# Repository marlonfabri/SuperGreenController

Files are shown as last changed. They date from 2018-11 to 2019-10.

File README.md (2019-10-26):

SuperGreenLab

SuperGreenLab (https://www.reddit.com/r/SuperGreenLab)

# Table of Contents

   * [SuperGreenController](#supergreencontroller)
   * [Board Overview](#board-overview)
   * [Outputs](#outputs)
      * [Light and AC](#light-and-ac)
      * [Motors](#motors)
      * [Sensors](#sensors)
      * [Power considerations](#power-considerations)
   * [License](#license)
   * [Creative Commons Warranties Disclaimer](#creative-commons-warranties-disclaimer)

# SuperGreenController

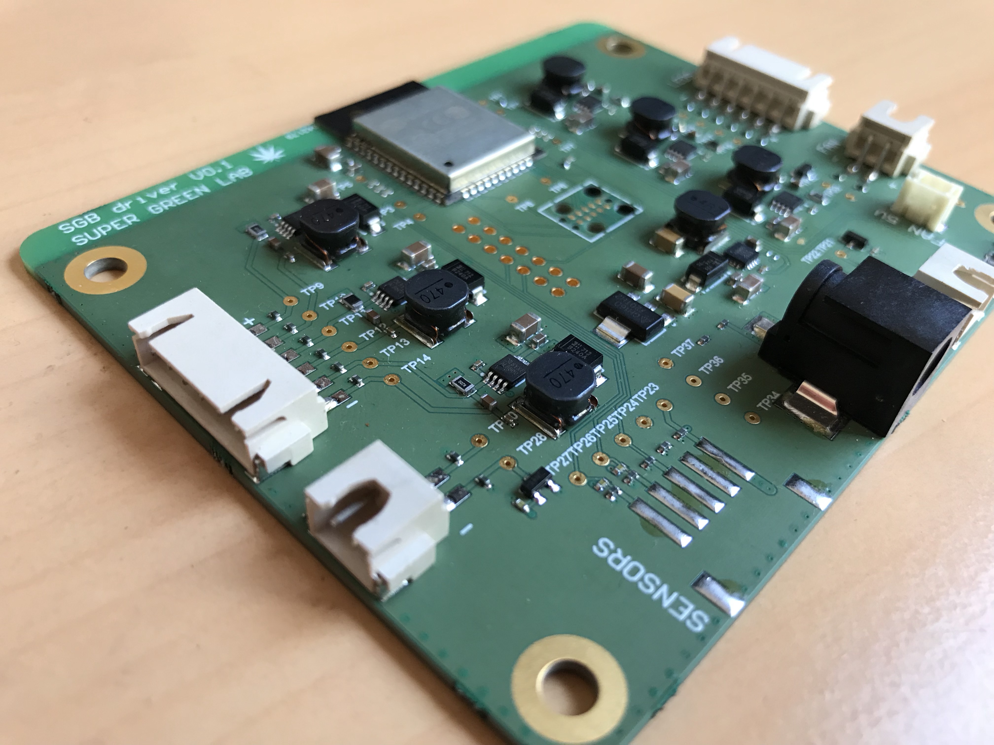
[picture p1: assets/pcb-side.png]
SuperGreenLed

V1.0 Prototype

Connected grow box controller with 6 light/AC control output (10V analog), 3 Motors output (24V/1A) and 3 sensors ports (I2C) from supergreenlab (https://supergreenlab.com/). This open hardware design is licensed under the Creative Commons Attribution-ShareAlike 3.0 Unported License.

Pull requests of relevant issues are warmly welcomed.

# Board Overview

* **MCU** : [ESP32-WROOM-32](https://www.espressif.com/en/products/hardware/esp-wroom-32/overview), wifi , bluetooth and BLE microcontroller. Fimrware : [SuperGreenOS](https://github.com/supergreenlab/SuperGreenOS) app : [SuperGreenApp](https://github.com/supergreenlab/SuperGreenApp)
* **Light/AC OUTPUTS** : 6x 0-10V Analog output (3.3V->10V done using [LM358](https://www.diodes.com/assets/Datasheets/LM358.pdf) op amp). Connector : [S3B-XH-SM4-TB](http://www.jst-mfg.com/product/detail_e.php?series=277)
* **MOTOR OUTPUTS** : 3x 24V output controlled by mosfet. Connector : [S2B-XH-SM4-TB](http://www.jst-mfg.com/product/detail_e.php?series=277)
* **SENSORS** : 1x I2C shared with embedded temperature sensor, 1x I2C shared on 2 connectors. Connector : [S4B-XH-SM4-TB](http://www.jst-mfg.com/product/detail_e.php?series=277)
* **POWER IN** : 24VDC/5A standard 5x2.5mm barrel/Jack input (Power supply : https://amzn.to/2DNSty4)
* **DCDC** : [TS30041](https://www.semtech.com/uploads/documents/ts3004x.pdf) 3.3V buck stepdown, up to 1A
* **ADDITIONAL** : 2.54 mm solderable header (additional pins and flash) JTAG and flash TAG connect interface
* **STACKUP** : standard 4 layers 1.6mm FR4 (Signal-GND-POWER-Signal)
* **SIZE** : 100mmx80mm

# OUTPUTS

## Light and AC

* **L1->L4** : Provide both power (24V) and control (0-10V). These outputs can be used to power SuperGreenBoards 36.301B (20W) and 72.301B (40W) for a max power consumption of 80W.
* **L5 & L6** : Power pin is not connected, only provide control (0-10V).

The 0-10V Analog output the Light/AC output can :
* Control any of the SGB 36.301B, 72.301B, 144.301B 
* Control a MeanWell type B or AB power supply (eg for the SGB 288.301B)
* Control any AC equipement through a [SSR relay](https://amzn.to/2DSlBoa)
* Control any device that can be driven by a 0-10V voltage

## Motors

**M1->M3** connectors are standard 2 pins JST connectors. It can be used to power 24V fans, blowers, pumps ect...

Example of compatible devices : [120mm blower](https://amzn.to/2GQcyqW) [97mm blower](https://amzn.to/2XcGl2I) [120mm fan](https://amzn.to/2GyCE26) [80mm fan](https://amzn.to/2IyqqZ4) 

## Sensors

* **S1** : 3V3 I2C port shared with embedded temperature/humidity sensor
* **S2 & S2bis** : shared 3V3 I2C bus

# POWER CONSIDERATIONS

The SuperGreenController is meant to be powered by a 24VDC/5A power supply for a total of 120W maximum.

A **10W** margin should be kept to ensure proper functionnement of the controller (this includes wifi, onboard sensors, onboard energy conversions ect.. and a large safety margin).
No more than **80W** of leds should be powered by the controller itself (2x 72.301B, 4x 36.301B or 1x 72.301B and 2x36.301B)
The rest of the energy can be used to power fans blowers and pumps.

An onboard current sensor will be used to monitor the power consumption of each device attached to the controller and determine is the power demand of the system is too high.

# License

This work is licensed under the Creative Commons Attribution-ShareAlike 3.0 Unported License. To view a copy of this license, visit http://creativecommons.org/licenses/by-sa/3.0/ or send a letter to Creative Commons, PO Box 1866, Mountain View, CA 94042, USA.

# Creative Commons Warranties Disclaimer

UNLESS OTHERWISE MUTUALLY AGREED TO BY THE PARTIES IN WRITING, LICENSOR OFFERS THE WORK AS-IS AND MAKES NO REPRESENTATIONS OR WARRANTIES OF ANY KIND CONCERNING THE WORK, EXPRESS, IMPLIED, STATUTORY OR OTHERWISE, INCLUDING, WITHOUT LIMITATION, WARRANTIES OF TITLE, MERCHANTIBILITY, FITNESS FOR A PARTICULAR PURPOSE, NONINFRINGEMENT, OR THE ABSENCE OF LATENT OR OTHER DEFECTS, ACCURACY, OR THE PRESENCE OF ABSENCE OF ERRORS, WHETHER OR NOT DISCOVERABLE. SOME JURISDICTIONS DO NOT ALLOW THE EXCLUSION OF IMPLIED WARRANTIES, SO SUCH EXCLUSION MAY NOT APPLY TO YOU.

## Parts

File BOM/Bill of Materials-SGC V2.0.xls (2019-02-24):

Comment | Description | Designator | Footprint | LibRef | Manufacturer | Manufacturer Part Number | Quantity
10uF | Multilayer Ceramic Capacitors MLCC - SMD/SMT 10uF 50V X5R +/-20% 1206 Gen Purp | C1, C4_L1, C4_L2, C4_L3, C5_L1, C5_L2, C5_L3, C6 | 1206 | C 10uF 50V X5R +/-20% 1206 Gen Purp | Taiyo Yuden | UMK316BBJ106ML-T | 8.0
0.1uF | Multilayer Ceramic Capacitors MLCC - SMD/SMT 100nF 50V X7R 10% | C2, C3, C7, C11 | 0603 | C 0.1uF 50V X7R 10% | Yageo | CC0603KRX7R9BB104 | 4.0
22uF | Multilayer Ceramic Capacitors MLCC - SMD/SMT 0805 25Vdc 22uF X5R 20% | C8, C9 | 0805 | C 22uF 25V X5R 20% | Murata Electronics | GRT21BR61E226ME13L | 2.0
22nF | MLCC - SMD/SMT 0.022uF 50V X7R 10% 0402 | C10 | 0402 | C 22nF 50V X7R 10% 0402 | Taiyo Yuden | UMK105B7223KV-FR | 1.0
MBR230LSFT1G | Schottky Diodes & Rectifiers 2A 30V SCHOTTKY | D1 | SOD-123LF | MBR230LSFT1G | ON Semiconductor | MBR230LSFT1G | 1.0
TAG connect |  | J1 | TC2050-IDC | TC2050 |  |  | 1.0
Header 2.54 |  | J2 | Pin header 2.54 14 contacts 2 rows | Header 2.54 |  |  | 1.0
JST XH3 |  | J3_L1, J3_L2, J3_L3, J4_L1, J4_L2, J4_L3 | JST XH-3 Right angle -SMD | S3B-XH-SM4-TB |  |  | 6.0
JST XH 2 |  | J5_M1, J5_M2, J5_M3 | JST XH-2 Right angle -SMD | S2B-XH-SM4-TB |  |  | 3.0
BARREL | CONN PWR JACK 2.5X5.5MM SOLDER | J6 | PJ-036BH-SMT-TR | PJ-036BH-SMT-TR | CUI Inc. | PJ-036BH-SMT-TR | 1.0
JST XH4 |  | J7_S1, J7_S2, J7_S3 | JST XH-4 Right angle -SMD | S4B-XH-SM4-TB |  |  | 3.0
APFA3010SEEZGKQBKC | Standard LEDs - SMD 3.0x1.0MM RA RGB SMD | L1 | APFA3010SEEZGKQBKC | APFA3010SEEZGKQBKC | Kingbright | APFA3010SEEZGKQBKC | 1.0
4.7uH | Fixed Inductors 8030 4.7uH 28.6mOhms +/-20%Tol 3600mA | L2 | 8030 | NRS8030T4R7MJGJ | Taiyo Yuden | NRS8030T4R7MJGJ | 1.0
DMN3404L-7 | MOSFET N-CHANNEL ENHANCEMENT MODE | Q1_M1, Q1_M2, Q1_M3 | SOT23 | DMN3404L-7 | Diodes Incorporated | DMN3404L-7 | 3.0
10K | Thick Film Resistors - SMD 10K OHM 1% | R1, R2, R6_L1, R6_L2, R6_L3, R7_L1, R7_L2, R7_L3, R10_L1, R10_L2, R10_L3, R11_L1, R11_L2, R11_L3, R12_L1, R12_L2, R12_L3, R13_L1, R13_L2, R13_L3, R14_M1, R14_M2, R14_M3, R15, R19, R20, R21, R22 | 0603 | R SMD 10K 1% 0603 | Yageo | RC0603FR-0710KL | 28.0
1R | Thick Film Resistors - SMD | R3 | 0603 | R SMD 1OHM 1% | Yageo | AF0603FR-071RL | 1.0
DNP |  | R4, R16, R23 | 0603 | R DNP |  |  | 3.0
68R | Thick Film Resistors - SMD 68 OHM 1% | R5 | 0603 | R SMD 68 OHM 1% | Yageo | RC0603FR-1068RL | 1.0
20K | Thick Film Resistors - SMD 20K ohm 1% 75V General Purpose | R8_L1, R8_L2, R8_L3, R9_L1, R9_L2, R9_L3 | 0603 | R SMD 20K ohm 1% 75V General Purpose | Yageo | RC0603FR-1020KL | 6.0
2.49K | Thick Film Resistors - SMD 2.49K OHM 1% | R17 | 0603 | R SMD 2.49K OHM 1% | Yageo | RC0603FR-072K49L | 1.0
0.02R | Current Sense Resistors - SMD 0.02 ohms 1% 75ppm AEC-Q200 | R18 | 2512 | R SMD 0.02 ohms 1% 75ppm | Yageo | PA2512FKM7W0R02E | 1.0
KSS221GLFS | Tactile Switches SPST NO-G LEAD 200g | SW1 | KSS221GLFS | KSS221GLFS | C&K | KSS221GLFS | 1.0
TP |  | TP16, TP17 | Test Pad | TP |  |  | 2.0
ESP-WROOM-32 |  | U1 | ESP-WROOM-32 | ESP-WROOM-32 |  |  | 1.0
LM358S-13 | Operational Amplifiers - Op Amps Low Power Dual OP AMP 100 dB | U2_L1, U2_L2, U2_L3 | SOP8 | LM358S-13 | Diodes Incorporated | LM358S-13 | 3.0
TS30041-M033 | Switching Voltage Regulators 1A 3.3V Current-Mode Sync. Buck Converter | U3 | QFN 3x3 16 | TS30041-M033QFNR | Semtech | TS30041-M033QFNR | 1.0
ZXCT1110W5-7 | Current & Power Monitors & Regulators LOW PWR HIGH-SIDE 24V 3uA MONITOR | U4 | SOT25 | ZXCT1110W5-7 | Diodes Incorporated | ZXCT1110W5-7 | 1.0
SHT30-DIS-B | Board Mount Humidity Sensors RH Accuracy +/- 3% Digital, DFN Type | U5 | QFN127P600-8N | SHT30-DIS-B | Sensirion | SHT30-DIS-B | 1.0
EZJ-Z0V650DA | Varistors 0402 40V 27pF | V1, V2, V3_L1, V3_L2, V3_L3, V4_L1, V4_L2, V4_L3, V5_L1, V5_L2, V5_L3, V6_L1, V6_L2, V6_L3, V7_L1, V7_L2, V7_L3, V8_L1, V8_L2, V8_L3, V9_M1, V9_M2, V9_M3, V10_M1, V10_M2, V10_M3, V11, V12, V13_S1, V13_S2, V13_S3, V14_S1, V14_S2, V14_S3, V15_S1, V15_S2, V15_S3, V16_S1, V16_S2, V16_S3 | 0402 | EZJ-Z0V650DA | Panasonic | EZJ-Z0V650DA | 40.0

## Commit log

2018-11-06 added schematics
    [Bill of Materials-SG driver.xls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]
2018-11-06 changed schematics file name
2019-01-11 added reddit button
2019-02-19 update board features
2019-02-24 pushed V2.0
    [Bill of Materials-SG driver.xls, Bill of Materials-SGC V2.0.xls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]
2019-03-01 changed driver to controller
